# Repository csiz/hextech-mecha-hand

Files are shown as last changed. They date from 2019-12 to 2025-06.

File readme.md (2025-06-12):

Hextech Mechahand
=================

Full range of motion robotic hand with pressure, position and force sensors for $300 bill of materials.

Mechahand mk 14
---------------

Working on release candidate mk14. Using own motor drivers for fine force control, enhanced 
integrated sensor suite, completely refactored control code, easy USB connection, and 
improved manufacturing and repairability.

Mechahand mk 12
---------------

Patented design with integrated sensor suite! [GB2626014](https://worldwide.espacenet.com/publicationDetails/originalDocument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)

Mechahand mk 10
---------------

New design routes all cables and tendons through the center of the wrist, hiding them from
view and increasing the range of movement.

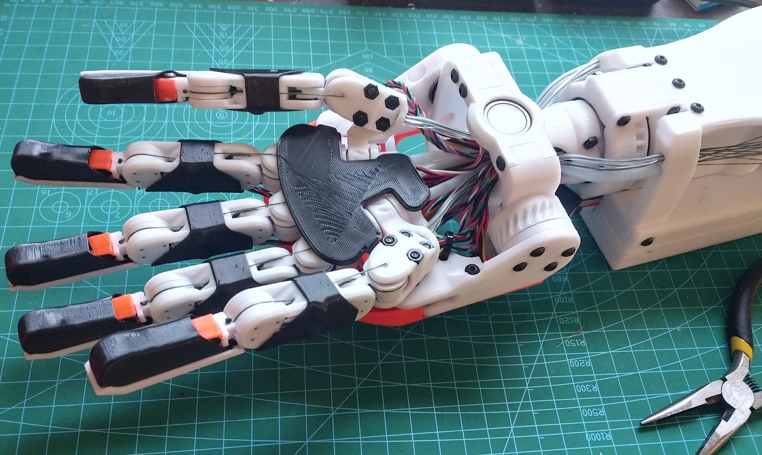
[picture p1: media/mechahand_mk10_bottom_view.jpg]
Mechahand mk 10.


Mechahand mk 9
--------------

Video of mk 9 picking up squish toy.

The Hextech mechahand is designed to be a low cost robot hand with a similar range
of motion as a human hand. It's targeted as an accessible standard for reinforcement
learning research. It has 20 degrees of freedom with position and force feedback on
each joint. The position encoders are placed in-situ allowing for accurate sensing
of the hand state regardless of the stretch on the tendons. Additionally there are
6 pressure sensors in the finger tips and palm for finer feedback. All electronics
plug into a compact PCB with current sensing for each actuated joint. The hand can
be controlled remotely by wifi using a force-limited PID loop. In the video, it's
mimicking my hand position in order to grasp an object. For autonomous control, a
custom force aware loop can be implemented.

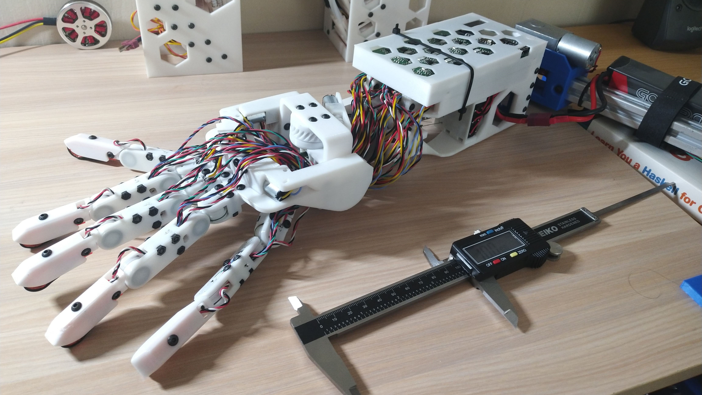
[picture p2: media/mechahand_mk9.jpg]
Mechahand mk 9.


The hand is built using off the shelf components and a 3D printed body at an amortized
cost of 300 USD per hand, requiring 30 hours of assembly time. Included in the cost
is the custom PCB designed for automated assembly. All design files for the mechanism,
the control circuit, and driver code is open source. Please open an issue wherever
[build instructions](build-instructions.md) need to be clarified.

Project layout
--------------

The project contains code for a 24 channel driver, the 3D printable model of the hand, and code to control the hand with a leap sensors. Details in the readme file of each folder.

* 24driver: Code and circuit design for a 24 channel PID controller with wireless interface and 12 pressure sensor inputs.
* hand_model: 3D model and instructions for the mecha-hand versions.
* leap_control: Code to control the hand via the leap motion sensor.

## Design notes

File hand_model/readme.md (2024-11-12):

Physical Mechahand Model
------------------------

1. No files for first iteration of mechahand, see [blog post](http://calin.mocanu.info/2019/06/11/mechahand-assemble.html) for pictures.
2. Mechahand II, the smallest hand version, failed due to pulley system cables passing through sharp corners. Can't have the cables passing through any corner as tensioning that wire causes large friction increase and a lot of plastic deformation of the nylon wire.
3. Mechahand III, the hand with the motors directly in the palm, failed because it's way too big and flimsy. Can't put motors on the fingers because they end up being too heavy and too big. Not way to cramp them tighter either. The 3rd version has a very modular design with each finger segment and wrist joint taken from 2 joint modules. Motorzied bigjoint is a sturdy and higher reduction joint for the wrist assembly. Motorized minijoint are perpendicularly geared joints as small as I can make with 1 motor and 1 potentiometer. Modularizing the hand was a good idea, and bigjoint is used in later versions.
4. Mechahand IV, first fully functional version, blog post pending. Uses the motorized bigjoint module for the wrist. There are direct drive joints with in-situ motors for the thumb and pinky opposable finger grasp. The rest of the fingers are controller by 1-sided pulley system; with the other side being a passive spring. With 2-sided pulleys on the old versions, there isn't enough tension on the string to gracefully unwind the side opposite the movement direction. We end up with loose wire coming out of the motor system and tangling up. There's no way to fix it without unreasonable tension on both sides. I therefore choose a single side pulley with a passive spring which keeps the system always in tension. We only need to be careful not to unwind when there's an external blocker.
5. Mechahand V, with neat finger shrouds! Fingers actuated again from 2 sides using the double pulley. Finger covers can hide the wiring to make it prettier. Using silicon wires leading to the motor system with a plastic soldering helper. Much neater to solder together, though putting the wires in place is difficult. Ok design on first sight, but multiple problems make it unusable. The little tubes are to stiff for the sideways finger wiggle. The printer springs are much too strong and have very little give. Difficult assembly requires a lot of force and moving about to get it to clamp down. When the clamp releases the spring fully extend and because the PTFE compression is too much. Overall too much friction to move the fingers when fully tensioned, and too little give in the tensioning system. Shrouds cover the wires though, will keep those. But thicker and mounted with screws so they can be used effectively.
6. Mechahand VI. First build and maybe usable hand! replaced the 6 to 1 buncher with 3 tube pairs that bunch into a single thick-ish tube leading to each joint. Also using much smaller springs for tension, this time acting directly on the tubes making a sort of piston. Neat, and mostly keeps the lines tensioned, but sometimes the spring goes in the tube, also small springs make for little give. Also have nicer tying mechanism on the nylon wire using a buckle of sorts. Pressure tip simplified for assembly by needing gauges on a single side that bends into an S shape. Sturdier finger covers too. Using the same soldering helper as V, but with thinner silicon wires. Unfortunately the wrist joint is propped stuck because of the large number of stiff PTFE tubes going to the fingers. The middle finger is also hard to bend because of the tube going to the tip joint. It's also hard to get consistent tension on the springs. If tensioned too hard it becomes stuck. Also because of the PTFE stiffness the 2 sides of a joint don't tension independently, which is the primary reason for the tensioning system, to prevent an unwind on the side that's relaxing.
7. Mechahand VII. Direct nylon pathing through center of joints. This design ditches the PTFE guides in favour of the direct pathing. Though still using the thick PTFE tube as a make shift piston for the new tensioning system. Instead of pushing 2 guide tubes apart, we now pull 2 end of the wire together. The wires slide past eachother to compress on a spring, guided by the thick PTFE tube and some plastic bits. Works with the long and easy to compress springs. When the plastic bits touch we also stop compressing the spring and can pass the full motor tension. Large springs means a large give, but hopefully not too much tension on the relaxing side. Can't test this hand until fully designed due to the tension being held by the hand structure. The hand structure is made much more rigid using proper bearings and thick plastic construction. Wrist pivots on bearings on both sides for structural integrity. Wrist roll now has the position potentiometer on a gear, and a large channel through the middle for the tendon wires. Removing battery from hand case, assuming external power source. Also to conserve space as new motor arrangement needs a lot of middle space for the tensioners. However no space on the side needed for the tensioning guides. Dropping the soldering helper in favour of dupont connectors for the fingers, and direct soldering for the motors. The extra connectors on the finger should help with assembly, as the finger cables can be separated from the motor.  Thicker plastic parts make for sturdier looking aesthetics, also the base cover. The middle covers, are also above some nuts and bolts and as packed as they can be, allowing for movement. Fingers crossed!
8. Mechahand VIII. Upgrade of mk 7 to fix weak wrist printing direction and thumb/pivot placement. Modified pivot worm joints to have a hole in the middle, like the wrist, to allow placing in line with the ring and index fingers. Much stronger placement, and keeps the distance between thumb/pinky and the wrist center constant; this is important to keep the tendons constant length. The ring finger is now fixed on the palm, as pivoting it together with pinky makes the leverage too large, and placement inconvenient. New placement also fixes the clearance issue with mk7. First hand version that really works!
9. Mechahand mk 9. Iterating on mk 8. Fingers now smaller and with integrated cover for the middle. The distance between the yaw and pitch joints halved to 15mm, making the joint closer to a ball joint. Unfortunately a true ball joint would require too much vertical thickness. Exploring design with magnetic sensors, but skipping for now. Thumb and pivot worm joints now smaller with lower gear ratio and bigger bearings. The 9mm bearings seemed like the weak points in previous design, hopefully now it's fixed. With smaller fingers, they are easier to place in the wrist and allows for nicer, smaller construction. Finger wires now go on the top, clearing the grasp of wiring. Wiring might look ugly as there's no hole to put them through, but placed mounting holes for an eventual cover. Finally tensioning using extension springs with a piece of nylon tied between the ends to cap the extended length. To pre-tension the tendons, we use the finger side loop of the spring as the hitch and the small buckle for simplified knotting; as an alternative to the hitch knot which doesn't hold on the thick nylon.
10. Mechahand mk 10. Pretty, buildable, and structurally sound mechahand! PTFE tubes brought back, but a short length passing through the wrist center needing minimal bending during wrist and thumb pivoting. Point of the tubes is to allow tendon tying from the outside, easing the build. Wrist hole substantially enlarged, allowing all electric cables and the tendon guides through. Designed ornate cover to hide wires. Designed tight-fitting skin out of TPU for the tip and mid finger, protects potentiometer cable connections, make hand grippier, neater! Bottom of fingers covered with a pressure sensor. Fingers shortened by 1cm, to near anatomical length. Moved case on top of wrist motor, compacting it by a bit. Should be a very presentable hand! (Spoilers... it was not presentable)
11. Mechand mk 11. New concept to integrate sensors in the palm and fingers. Designed a flexible circuit that folds into the hand shape and has integrated magnetic rotation potentiometers on the joints and pressure sensors on the fingertips. Now this is a presentable hand! The fingers are assembled from two parts that mesh with eachother and are held together by the flexible skin. The circuit is simply placed inside channels in the fingers and held in place by little clips. The wrist area now uses individual PTFE tubes for each actuated joint and there are indents designed into the palm and motor box to place the guide tubes. Still a lot of pain to assemble, the guide tubes rub on eachother as the wrist bends and might tangle the cable connection. The wrist stiffens up with the guide tubes in place and the tendons tensioned up... Unfortunate, but the flexible circuit with integrated sensors is a great idea!
12. Mechahand mk 12. Slight improvements to finger design to ease up assembly and strengthen weak points. Switching to coreless motors for quieter operation (true!). Now designing channels into the plastic of the motor box to guide the tendons directly but smoothly to each corresponding motor. Replaced the guide tube idea with directly connecting the tendons from motor box to the palm, however they pass through PTFE rings in the center of the wrist and at the beggining of the motor box to minimize friction and minimize the change in tendon length as the wrist bends. Unfortunately tensioning up the finger tendons now forcefully pulls the wrist to one side, and the motors are unable to overcome. The wrist was redesigned with bevel gears (partially filled with gear teeth) for easier assembly than the purely wire driven differential. Also using bevel gears for the finger pivot action, again for ease of assembly. Electric wire now shielded by a flexible plastic channel when passing through the wrist channel.
13. Mechahand mk 13. Changing from double sided tendons for the finger joints to single side tendon for flexion and spring for finger extension. Switching the knuckle actuation from actuating the pitch and yaw separately to actuating both diagonally (similar to the differential). Big improvement in precision after this change, although more complex driving mechanism to avoid unspooling! More improvement to finger design, thickenned up fingers for strength and created stubbier finger models for the thumb and pinkie. Changed palm design to also use springs for the pivot actions and enlarged the top cover to cover everything nicely. Solved the wrist guide problem by designing a guide channel made of stiff segments with channel holes held together by a flexible snake connecting the motor box and palm. The flexible core forces the guide plates into bending smoothly with the movement of the wrist. This wrist design finally has the full range of movement that it was designed for and is able to move when the fingers move (not locked in place by the tendon tension). Also, since the fingers are driven from a single side, the bias on the wrist from the finger actuation is more predictable. This robot hand works!

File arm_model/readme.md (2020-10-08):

Hextech Mecharm
===============

4 DOF robotic arm to drive the upper arm half of the robot hand. Ball like joint using
a differential gear on the shoulder, separate motor for arm twist motion, and another
motor for the elbow. Using 3D printed cycloidal drives and a 5010 brushless motor used
in large drones, but low 360KV.

TODO:
-----
[ ] Fix elbow motor, I think star connection not properly soldered.
[ ] Place and wire potentiometers too.
[ ] Drive motors using the RTM library of the ESP32.

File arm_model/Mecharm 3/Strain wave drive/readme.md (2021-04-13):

Strain wave drive
-----------------

Backdriveable strain wave drive with 30x and 42x reduction ratios.

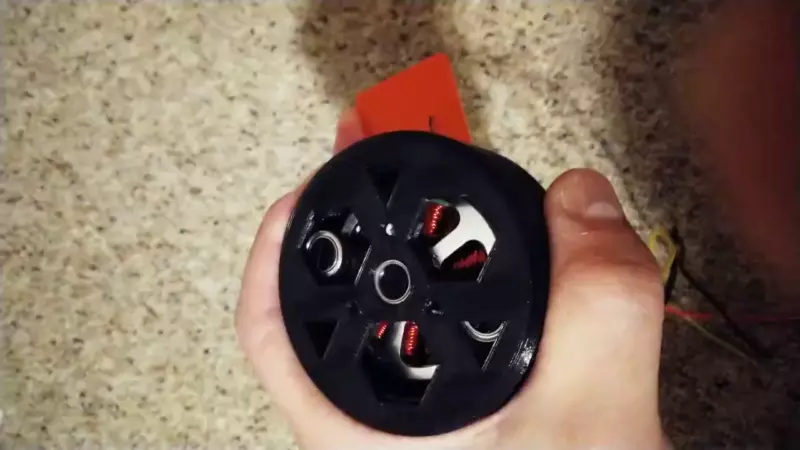
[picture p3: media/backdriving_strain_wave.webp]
Video of strain wave being rotated manually.


Compact construction with flex spline cup surrounding the motor. Drive size is 70mm diameter and 32mm height. Printed in PETG, including the flex spline.

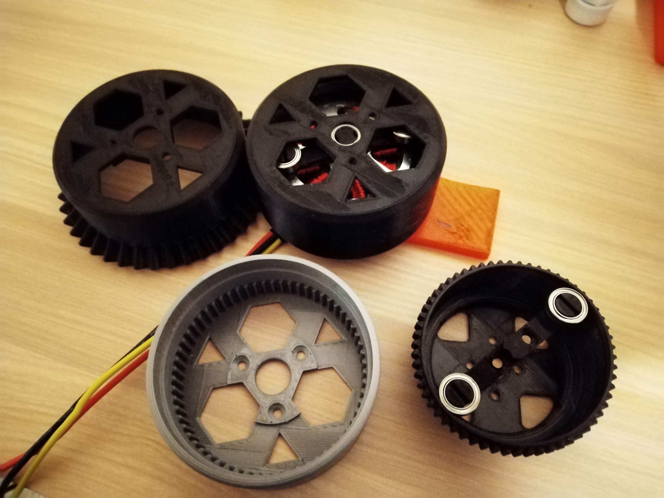
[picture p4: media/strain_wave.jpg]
Strain wave drive.


Components:
  * 1 - 5010 brushless motor
  * 1 - 6810 ball bearing
  * 3 - MR128 ball bearings

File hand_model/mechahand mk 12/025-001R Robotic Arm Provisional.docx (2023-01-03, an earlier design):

UNITED STATES PROVISIONAL PATENT APPLICATION

of

Calin Mocanu

for

A SYSTEM OF ROBOTS AND ROBOTIC PARTS INCLUDING METHOD OF CONSTRUCTION AND METHOD OF USE

A SYSTEM OF ROBOTS AND ROBOTIC PARTS INCLUDING METHOD OF CONSTRUCTION AND METHOD OF USE

FIELD OF THE INVENTION

[001] This application relates to the design and construction of robotic parts, and more particularly, improvements in functionality and improvements in compact designs for robotic parts.

# BACKGROUND OF THE INVENTION

[002] Humans have been trying to create robots for decades, but with only limited success. Robotic parts such as arms, wrists, and hands suffer from a number of drawbacks and limitations. One of the drawbacks in the field of robotics currently is a limitation on the ability to reduce the size of various features.
[003] As an example, small jointed parts like fingers need to carry numerous sensors, such as pressure sensors joint position sensors, etc. And, in addition to the sensor itself, each sensor has various wires, wiring harnesses, connectors, etc. that must be carried through the fingers, including tight places like knuckle joints. As used herein, the term “wire” can refer to single strands or multiple-strand wires that are insulated with insulating material surrounding the conductive strand(s). The insulating material around the strand is flexible, and the strand with the insulation around it can be bent into various paths throughout an electronic device. However, the strand plus the insulating material around it that form a wire can become bulky when multiple wires are used in the same device or routed along the same path. The terms “wiring harness” can refer to physical connectors that allows two insulated wires to be connectively joined to form a single electric conductor through the use of Newtonian force, including connectors that can connect multiple sets of insulated wires at the same time. Wire harnesses are typically made of insulated metal wires that must be attached to connectors on both sides. The wire harness can then be plugged into corresponding connectors on two circuits, connecting them electrically. This requires that both wires have a connector or harness. These harnesses or connectors can be clips mounted at the end of the conductive strands so that a user can forcefully engage two clips or other connectors together to form a conductive strand that conducts electricity and electric signals through the clip from one strand to the other, thereby forming a single conductive path. To join two wires into a single conductive path, a wiring harness must be applied to both wires, which can be a costly and difficult step in manufacturing as the insulation must be stripped from the end of the wire, the wire must be connected to the harness, etc. For each connection end the electrical insulation must be stripped, then the wire is crimped into pins, then the pins must be inserted into the plastic male connector. This must be done for every end of every wire.
[004] These connections where the end of the wire is connected to a wiring harness create a weak point along the electrical path, and as the wire is flexed back and forth repeatedly in normal usage, the wire is most likely to break at the connection with the wiring harness that allows the two wires to be joined. The places where the wires connect to the harnesses tend to see the most stress, and the wires tend to fail at the places where they are connected to the harnesses. Furthermore, after the two harnesses are linked together, they take up a large amount of space inside the device. When this is multiplied by a large number of wires, the result is either a large number of bulky wires and wiring harnesses that must take up space, or a smaller number of larger multi-wire harnesses that take up more space.
[005] A highly functional robot finger would ideally be able to sense pressure at the tip of the finger, the back of the finger, both sides of the finger, and of course, the inner finger pad where the finger makes contact with an object being gripped by the robot’s hand. However, this requires a multitude of bulky sensors, wires, wiring harnesses, and circuit connectors, that must all be packed into a small finger, while also allowing the finger to bend and move. This means that parts such as fingers must be at least a minimum size that is often larger that desired for various applications. Furthermore, as the manufacturer attempts to reduce the overall size of the finger to the minimum size capable of carrying all of the necessary components, the space inside the finger gets more and more crowded, and therefore more and more difficult for the manufacturer to assemble all of the components inside of the tight space. All of this contributes to ever increasing costs as manufacturers attempts to reduce the size of various parts given the constraints of current technology.
[006] In some cases, in order to reduce the size of the fingers, it has been necessary to reduce the number of sensors, the quality of sensors, and/or the types of sensors. This means that there is often a direct correlation between decreasing size of parts such as fingers and decreasing functionality. Manufacturers may also reduce the quality or strength of other parts such as fingers and wrists in order to allow for decreased size, but this decreases in quality, such as decreasing the robustness of hinges and hinged parts, results in inferior products that break easily.
[007] In some cases, the size has been reduced by attempting to remove some components such as sensors from tight parts such as fingers. This can be reducing the number of pressure sensors, but can also mean attempting to measure certain variables such as fingertip position from alternate locations outside of the fingertip. For example, some manufacturers have attempted to measure finger position by placing magnets in the finger tips, and then sensing the proximity of the magnet to other parts such as a palm of a robotic hand. Moving the sensing activity to the palm means there is more space for these sensors. However, this also results in a significant reduction in quality. Placing magnets in the fingertips can have an effect on the robot’s ability to grasp and release magnetic objects, but even worse, grasping and releasing magnetic objects will interfere with the sensor’s ability to accurately know where the fingertips are positioned. Furthermore, although ample space may exist in a palm area, magnets in the fingertips take up valuable space used for pressure sensors and may interfere with the remaining pressure sensors.
[008] Other manufacturers have attempted to measure position by monitoring the positions of servos in the arm that control the fingers through tendons. However, this can be extremely unreliable. The tendons that connect to the finger tips can stretch over time, resulting in inaccurate readings, and as the tendons pass through the narrow and crowded finger knuckles, even slight interactions with other components such as wires and wire harnesses can lead to inaccurate results. As wires and wiring harnesses interfere with the path of the tendons, the length of tendon does not exactly correlate to finger position. In the state of the current technology, measuring the position of the fingers by monitoring the rotational position of the servos in the arm that drive the fingers is the best option, given that the measuring can occur outside of the finger and reduce the size constraints of a finger, but this method of measuring finger position is prone to inaccuracy.
[009] Various other means also exist for more accurately measuring the rotational position of the joints, and therefore the position of the fingertip, or wrist, or arm, etc. However, to date, either these means produce inaccurate results or have not been reduced in size sufficiently to allow their use in a robotic finger knuckle that can be the size of a human finger while also allowing for tendons wires, and wiring harnesses to exist in the same space.
[0010] Up to now, there has been a trade off between various aspects, including the quality of sensing, the number of sensors and the amount of sensed data, the size of the finished parts, and the cost to assemble. For example, as size decreases, the quality of components such as sensors and/or the number of sensors decreases and/or the cost of assembly increases. Furthermore, there are hard limits on the ability to reduce size while still maintaining even a minimum level of sensing at any cost. The same can be said about improving the quality and/or number of sensors, which then increases size and cost, and the same can be said about reducing cost which then results in reduced sensing and increased size. Similarly, the quality of parts such as fingers and wrists can be part of the trade-off, and reducing the robustness of components such as hinges and knuckles can allow for reduced size, but with a corresponding reduction in quality. Improving one of these aspects seems to come at the cost of the others.
[0011] It would be desirable to have new robotic technology and new components that allow robotic parts such as fingers, wrists, arms, etc. to be reduced in size to the size of human fingers, wrists, arms, etc, or smaller, while also maintaining robust pressure sensing and position sensing, reducing costs, and maintaining strong parts and components. It would be further desirable if the new robotic technology and new parts result in reduced cost of components and reduced cost of assembly while also allowing for reduced size at the same time.

# SUMMARY OF THE INVENTION

[0012] This invention overcomes disadvantages of the prior art by providing a system and method for manufacturing robotic parts, including parts that can be analogous to fingers, hands and arms. The system and methods described herein include various ways to reduce the cost of manufacturing, reduce the size of manufactured parts, and increase the reliability and quality of sensed data. These improvements include producing capacitive pressure sensors that are simple in construction and can be manufactured by folding a sheet of material over itself to form a sandwich around a double-sided adhesive. These force sensors are simple and cheap to manufacture, and can be connected to cheap touch sensor chips. The sheet of material can also be a Flexible Circuit Board (FCB) that can connect the sensor to other electronic components, including touch sensor chips and processors. The touch sensor chips can be Integrated Chips (IC) that can be integrated on the FCB, and the IC(s) can be located near the force sensors on the FCB. The FCB can also include multiple sensors on the same FCB, so that, for example, multiple sensors in a finger such as finger tip, sides of the finger, back of the finger, etc, can all be manufactured as part of the same FCB, and can all be connected to the touch sensor chip(s) integrated on the FCB. With all of the sensors and circuits manufactured as a single FCB, the finger can be constructed with no wiring harnesses or other bulky connectors to be connected during manufacturing or taking up space inside narrow parts like a finger. The single FCB can then be arranged through a finger, including through narrow joints such as knuckles, and can be tied into place within a finger, held in place with clips, etc, and can connect sensors to a processor with very little space requirements, leaving space within a small finger for further components. Because the FCB is free from insulation, there is no rubber or other insulation within the fingers to get caught up on moving parts or prevent tendons from sliding freely. The flex circuit connectors can be printed in the same process required to make the circuit board. The connectors can be electrical traces as any other on the FCB, with exposed and plated pads on the end, using the same process used to make the pads of most components on the circuit board. The flex circuit can then be directly inserted into the female connector on the palm. The connector can also be thinner because the flex circuit is thinner than wire connectors.
[0013] Additionally, sensors such as rotational position sensors, also referred to as rotational encoders, can be configured to be integrated with the FCB, thereby eliminating the need for additional wires, wire harnesses, and other connectors. These rotational position sensors can be used to measure the rotational position of hinged joints such as finger knuckles. These sensors can utilize the Hall effect to measure the orientation of a diametrically magnetized magnet that can be assembled in a stack with the axis of the magnet on the same axis as the knuckles or other hinges. This approach with stacking a disc shaped magnet and rotational position encoder on axis with the knuckle hinge allows for a small and flat rotational sensor that takes up little space while still reporting rotational position with accuracy. The rotational sensor can also be configured to integrate with the FCB to provide measured data to the processor without the need for additional wiring. The space savings that result from the innovative design of this sensor combined with the space savings that result from the FCB replacing traditional connection types allows for the use of on-axis hall sensors which are significantly more accurate than prior art position sensors for robotic parts.
[0014] The use of this precise on-axis rotational position sensor also allows for the use of a 4-bar linkage system for torque sensing. The 4-bar linkage torque sensing system can allow a processor to calculate the pressure being applied to a held object by a finger. A processor can measure minute divergence, or flexing, of finger components by measuring and comparing the rotational position at multiple joints at the same time. As applied pressure increases, so too does the flex in certain components, which can be determined by measuring the rotational positions of multiple joints at the same time. The applied pressure can be determined from the amount of flex. Calculating the applied pressure when a fingertip is in contact with an object means that a pressure sensor such as a capacitive pressure sensor does not need to be used at the fingertip, thereby further reducing the space requirements in the finger while also decreasing production cost.
[0015] In an embodiment, a robotic component can include a FCB that can include at least one capacitive force sensor, the capacitive force sensor being unitary with the FCB, and the capacitive force sensor having two electrodes folded around a compressible dielectric pad, and at least one rotational position encoder, the rotational position encoder being on the FCB as an Integrated Chip (IC), and at least one magnet, the at least one magnet being embedded in a joint of the robotic component so that the at least one magnet and the at least one rotational position encoder are on-axis with the joint, so that the rotational position encoder can determine the rotational position of the magnet within the joint.
[0016] The FCB can include at least one strain relief loop that passes around a loop holder within the robotic component. The FCB can include at least one bending segment, the bending segment allowing the FCB to be folded into multiple planes. The at least one rotational position encoder can include at least two rotational position encoders, and wherein the FCB can be bent so that a first rotational position encoder is in a first plane and measures a rotational position around a first axis, and a second rotational position encoder is in a second plane and measures a rotational position around a second axis, wherein the first axis and the second axis are in different planes. The FCB can include at least one knot segment, wherein the knot segment is tied in a knot around a support within the robotic component. The joint of the robotic component can have a hollow central canal that passes through the center of the joint, including passing through the rotational axis of the joint, and wherein the FCB passes through the hollow central canal and the rotational axis of the joint. The robotic component can also include a layer of foil between the at least one capacitive sensor and the outside of the robotic component, the layer of foil shielding the capacitive sensors from external capacitance. The robotic component can include a 4-bar linkage system, wherein a motor that powers the movement of one joint will also power the movement of a second joint through the 4-bar linkage, and wherein a linkage bar can be semi-rigid, so that a quantity of force applied to a finger tip can be calculated from the rotational position of the two joints when the linkage bar is flexed under force. The FCB can be tied in a knot around the linkage bar. The joint of the robotic component can have a hollow central canal that passes through the center of the joint, including passing through the rotational axis of the joint, and wherein tendons that control the movement of the robotic component are routed through the hollow central canal and the rotational axis of the joint. The robotic component can have multiple FCBs in different portions of the robotic component, and the multiple FCBs can be connected together by FPC connectors and can be connected free of soldering or wiring harnesses. The FCB can include holes through the FCB and wherein tendons that control the movement of the robotic component can be routed through the holes through the FCB.

BRIEF DESCRIPTION OF THE DRAWINGS

[0017] The invention description below refers to the accompanying drawings, of which:
[0018] Fig. 1 is a perspective view of a robotic finger, according to an illustrative embodiment,
[0019] Fig. 2A is an upper perspective view of circuitry, including sensors, from inside the robotic finger of Fig. 1, according to an illustrative embodiment;
[0020] Fig. 2B is a lower perspective view of the circuitry of Fig. 2A also showing the position of knuckle magnets, according to an illustrative embodiment;
[0021] Fig. 3 is a top view of the circuitry of Fig. 2A, shown in a flat conformation before the sensors are folded and before the FCB is arranged into the shape used inside the finger of Fig. 1, according to an illustrative embodiment;
[0022] Fig. 4A is a side view of the circuitry of Fig. 2, showing pressure sensors folded into the sensing conformation, according to an illustrative embodiment;
[0023] Fig. 4B is a detailed view of the pressure sensors shown in Fig. 4A, according to an illustrative embodiment;
[0024] Fig. 4C is a cross sectional view of the sensors shown in Fig. 4A, taken along cross section line 4C-4C of Fig. 4A, according to an illustrative embodiment;
[0025] Fig. 5A is a bottom perspective view of a finger, according to an illustrative embodiment;
[0026] Fig. 5B is a side view of the finger of Fig. 5A, shown without the outer shell, according to an illustrative embodiment;
[0027] Fig. 5C is a cross section of the finger of Fig. 5B, taken along cross section line 5C-5C, and viewed from below, according to an illustrative embodiment;
[0028] Fig. 5D is a bottom perspective view of various components inside of the finger of Fig. 5A, including structural components, and showing the placements of magnets for rotational sensors, according to an illustrative embodiment;
[0029] Fig. 5E is a detailed view of the area of detail 5E in Fig. 5C, showing an arrangement of joint components within the bone, according to an illustrative embodiment;
[0030] Fig. 6A is an exploded bottom perspective view of various components inside the finger of Fig. 5A, including multipurpose clips that can maintain the positions of rotational sensors and the FCB; according to an illustrative embodiment;
[0031] Fig. 6B is a side view of various components inside the finger of Fig. 5A, showing rotational sensors held in place by the clips and showing the arrangement of the FCB and magnets; according to an illustrative embodiment;
[0032] Fig. 7A is a schematic diagram of a 4-bar linkage system that can use magnetic rotational sensors to determine torque and pressure, shown with the finger in a straight conformation, according to an illustrative embodiment;
[0033] Fig. 7B is a schematic diagram of the 4-bar linkage system of Fig. 7A, shown with the finger in a bent conformation and without applied pressure, according to an illustrative embodiment;
[0034] Fig. 7C is a schematic diagram of the 4-bar linkage system of Fig. 7B, shown with pressure applied to an outer, fingernail side of a finger, thereby flexing the linkage bar in a shortened conformation; according to an illustrative embodiment;
[0035] Fig. 7D is a schematic diagram of the 4-bar linkage system of Fig. 7B, shown with pressure applied to an inner side of a finger, thereby flexing the linkage bar in an elongated conformation; according to an illustrative embodiment;
[0036] Fig. 8A is a perspective view of the interior of the robotic finger of Fig. 8A showing the components of the 4-bar linkage system, according to an illustrative embodiment;
[0037] Fig. 8B is a top view of the partial robotic finger shown in Fig. 8A, according to an illustrative embodiment;
[0038] Fig. 8C is a cross section view of the partial robotic finger of Fig. 8B, taken along cross section line 8C-8C, showing the finger in a straight conformation, according to an illustrative embodiment;
[0039] Fig. 8D is a cross section view of the partial robotic finger of Fig. 8B, taken along cross section line 8C-8C showing the finger in a bent conformation, according to an illustrative embodiment;
[0040] Fig. 9 is a perspective view of an assembled robotic hand, including a wrist, palm, and fingers, according to an illustrative embodiment;
[0041] Fig. 10 is a perspective view of the circuitry, including sensors, from inside the robotic hand with fingers, according to an illustrative embodiment;
[0042] Fig. 11A is a perspective view of the circuitry, including sensors, from inside of a robotic palm shown without fingers, according to an illustrative embodiment;
[0043] Fig 11B is a top view of the circuitry of Fig. 11B, shown in a flat conformation before the sensors are folded and before the FCB is arranged into the shaped used inside the palm of Fig. 9, according to an illustrative embodiment;
[0044] Fig. 12A is an exploded perspective view of the top of a partially assembled palm, showing circuits, sensors, and removed back cover, according to an illustrative embodiment;
[0045] Fig. 12B is an exploded perspective view of a partially assembled palm, showing circuits, sensors, and removed hand bottom cover, according to an illustrative embodiment;
[0046] Fig. 13A is a partially assembled view of a hand, showing thumb and pinkie joints and thumb and pinkie joint rotational position sensors, according to an illustrative embodiment;
[0047] Fig. 13B is a detailed view of a pinkie joint of Fig. 13A, showing an arrangement of bevel gears, according to an illustrative embodiment;
[0048] Fig. 13C is a detailed view of the pinkie joint of Fig. 13B, showing a rotational position sensor within the joint, according to an illustrative embodiment;
[0049] 14A is a perspective view of the wrist of Fig. 9, showing the hollow central channel that can accommodate tendons and FCBs, according to an illustrative embodiment;
[0050] Fig. 14B is a perspective view of selected components within the palm of Fig. 12B and the wrist of Fig. 14A, showing bevel gear components, according to an illustrative embodiment;
[0051] Fig. 14C is an exploded view of the left bevel gear and outer structure of the wrist of Fig. 14B, showing a rotational position sensor; according to an illustrative embodiment;
[0052] Fig. 15 is a method of manufacturing a robotic finger, according to an illustrative embodiment;
[0053] Fig. 15B is a method of manufacturing a robotic hand, according to an illustrative embodiment;
[0054] Fig. 16 is a method of sensing force using a capacitive sensor, according to an illustrative embodiment;
[0055] Fig. 17 is a method of sensing force using rotational position sensors, according to an illustrative embodiment; and
[0056] Fig 18 is a schematic view of a robot control processor, according to an illustrative embodiment.

DETAILED DESCRIPTION

[0057] There are a great many possible implementations of the invention, too many to describe herein. Some possible implementations that are presently preferred are described below. It cannot be emphasized too strongly, however, that these are descriptions of implementations of the invention, and not descriptions of the invention, which is not limited to the detailed implementations described in this section but is described in broader terms in the claims.
[0058] As used herein, the term robotic finger refers to a robotic part that can include force sensors, joints, joint position sensors, and flexible circuit boards (FCBs). Although the robotic finger described herein is similar in appearance and function to a human finger, the technology described herein is not intended to be limited to human forms. Similarly, as used herein, the terms robotic hand, palm, and wrist refer to robotic parts that include force sensors, joints, position sensors, and FCBs, and although the robotic parts described herein are similar in appearance and function to the human body, the technology described herein is not intended to be limited to human forms.
[0059] Fig. 1 is a perspective view of a robotic finger, according to an illustrative embodiment. A robotic finger 100 can have a base 108, and multiple phalange segments including distal phalange 102, middle phalange 104, and proximal phalange 106. Phalanges 102 and 104 can be separated by joint or knuckle 112, and phalanges 104 and 106 can be separated by joint or knuckle 114. Knuckles 112 and 114 can bend or curl inward along arrow A and arrow B, respectively. Phalange 106 and base 108 can be separated by joint 116 that can bend or curl along arrow C, and phalange 106 and base 108 can also be separated by joint 118 that can bend or yaw along arrow D. Joints 116 and 118 allow phalange 106 to move relative to base 108 along two different axis. It should be clear that in various embodiments, larger or smaller numbers of phalanges are possible, with joints between each phalange, and it should be clear that any two phalanges can have one or more than one joint between them thereby allowing for one or more than one axis of movement between any two phalanges.
[0060] The design described herein allows for the finger, including joints, to have a very small form factor. In various embodiments, the finger, including joints, can have a maximum width FW of 16 mm or less. In various embodiments, the finger can have a maximum height FH of 18 mm or less. In various embodiments, a finger knuckle can have a maximum knuckle height KH of 20 mm. The reduced size is possible in part due to the absence of wiring and wiring harnesses throughout the finger, along with the compact design for the knuckle rotational position sensors. The finger can be fully functional with capacitive force sensors in four directions, knuckle rotational position sensors, and a torque force sensor, all within the compact design having a maximum finger width of 16 mm, a maximum finger height of 18 mm, and a maximum knuckle height of 20 mm.
[0061] In traditional designs, pressure sensors in a finger would require a separate sensor unit for each touch sensitive area, and each pressure sensor unit would have wires extending from the sensor so that each of the sensors can be connected to a controller. In some cases this could include bulky wiring harnesses or connectors. The design described herein has a number of pressure sensitive areas without the need for wires or wiring connectors. The finger 100 shown in Fig. 1 can have four pressure sensors that can sense pressure at pressure sensitive areas 122, 124, 126, and 128, however, different numbers and configurations of pressure sensors are possible.
[0062] Fig. 2A is an upper perspective view of circuitry, including sensors, from inside the robotic finger of Fig. 1, according to an illustrative embodiment, and Fig. 2B is a lower perspective view of the circuitry of Fig. 2A also showing the position of knuckle magnets, according to an illustrative embodiment. Finger circuitry 200 can include a finger FCB 202, finger tip force sensors 222, 224, 226, and 228, and rotational position encoders 212, 214, 216, and 218. As used herein, the terms “rotational position encoder,” “rotational encoder,” and “contactless potentiometer” can be used interchangeably. Finger tip sensor 226 can sense force on the back of the finger, in a location associated with a fingernail in a corresponding human finger, and finger tip sensor 224 can sense pressure on the distal tip of a finger tip. Finger tip sensor 222 can sense pressure on a first side of the finger, and finger tip sensor 228 can sense pressure on a second side of the finger, opposite from the first side. Although this description describes specific sensors in specific locations, and describes them in the context of similarity to human fingers and human sensing locations, it should be clear that this is merely illustrative, and various numbers and arrangements of sensors are possible.
[0063] Rotational position encoder 212 can sense the rotational position of the diametrically magnetized magnet embedded in the knuckle 112, and can therefore detect the rotational position of the knuckle 112. or put another way, can detect the angle of the joint between distal phalange 102 and middle phalange 104. Rotational position encoder 214 can sense the rotational position of knuckle 114 between phalanges 104 and 106. Rotational position encoder 216 can sense the rotational position of knuckle 116 between phalange 106 and base 108 as phalange 106 curls inward toward the palm, and rotational position encoder 218 can sense the rotational position of joint 118 as phalange 106 moves in a yaw direction relative to base 108. A diametrically magnetized magnet, such as diametrically magnetized disc magnet 232, 234, 236, and 238 can be positioned in each joint, and the encoder can detect the rotational position of the magnet. As used herein, the term “diametrically magnetized magnet” refers to a magnet that is magnetized across the diameter, with the poles located on the curved surfaces along the outer circumference of the magnet. The magnets shown in Fig. 2B are shown in proximity to the corresponding rotational encoders, however, it should be clear that the magnets are fixed within the joints and move with the joints relative to the encoders, so that the encoders can detect the rotational position of the magnets, and thereby detect the rotational position of the joints.
[0064] Taken together, the rotational position encoder and diametrically magnetized magnet form a rotational position sensor. The rotational position encoder can be an integrated chip (IC) on the FCB that can calculate and digitize the angle. The rotational position encoder can include 4 analog hall effect sensors arranged on the IC of the FCB in a circle around the axis center. The chip can interpolate the analog signals and perform basic trigonometric math right there on the IC. The output of the IC that is the rotational position encoder can be a digital angle, and that digital angle data can be transmitted through traces on the FCB.
[0065] The rotational position encoders and the force sensors can be integrated as part of the FCB. Integrating sensors such as sensors 222, 224, 226, and 228, rotational encoders 212, 214, 216, and 218 as part of the FCB allows for a design that is free from insulated wires and wiring harnesses. The FCB can include separate conductive traces for each sensor, including force sensors and rotational position sensors, and can connect each sensor to circuits and processors located outside of the finger without the need for additional connectors or wires within the finger. By having all of the sensors connected to circuits and processors outside of the finger through fine traces on a single FCB, the physical volume of all connections from sensors in the finger to connections outside of the finger is substantially reduced, allowing for much smaller form factor fingers, while also allowing for reduced assembly cost because all rotational encoders and force sensors in a finger can be already pre-manufactured together in a single finger circuit unit 200.
[0066] The FCB 202 can be routed through narrow spaces in an articulated finger, including though the narrow spaces inside a joint or knuckle. However, as different joints move and move in different directions, different forces can be exerted on the FCB in different directions. To overcome this problem, a series of strain relief loops can be folded into the FCB, such as strain relief loops 244, 246, and 248. These strain relief loops provide extra slack in the FCB, so that the overall length can lengthen and shorten as necessary, without the FCB getting tangled or getting in the way of other components. The loops can be wrapped around loop-holders (not shown) throughout the path of the FCB, including within the finger or other components, explained more fully below.
[0067] Additionally, the FCB can be tied in place, such as FCB knot 242. FCB knot 242 can be tied around a structural component (not shown) within the finger or other component, and can secure the FCB in place within the finger while the various finger components move in different directions and exert various forces on the FCB. In various embodiments, the knot 242 can be tied around a linkage bar within the finger, explained more fully below. Because the FCB itself is flexible and can be physically tied into a knot, it can be secured in place in a way that allows flexible motion of the finger and the FCB without the need for bulky attachment devices or circuit routing components.
[0068] Fig. 3 is a top view of the circuitry of Fig. 2A, shown in a flat conformation before the force sensors are folded and before the FCB is arranged into the shape used inside the finger of Fig. 1, according to an illustrative embodiment. Turning now to Figs. 1, 2A, 2B, and 3, strain on the FCB can further be reduced by having at least a portion of the FCB be split along the length, so that the FCB can more easily be flexed in different directions without bowing, binding, or kinking. Having a split 252 in an FCB 202 can be particularly valuable in places where multiple joints between the same segments allow for bending along different directions, or through three dimensions. By way of non-limiting example, the split 252 can allow a first side 254 to move and flex independent of second side 256. When proximal segment 106 moves along arrow C and along arrow D relative to base 108, the two narrower sides can move independently more freely and more flexibly compared to a single FCB having the combined width of 254 plus 256.
[0069] The FCB can be designed to fold into nearly any shape. As shown in Fig. 3, there can be one or more 90-degree turns such as 90 degree turn 282 before the FCB turns into two strands 254 and 256 that pass through the knuckles 116 and 118. Combined with a 90-degree bend at bending zone 284, the FCB path can route along the sidewall of the middle segment, then turn and route along a different direction through the knuckles 116 and 118. Similarly, 90 degree turn 286 and a 90 degree bend at bending zone 288 allow the FCB to exist in one plane in one place in the finger, and turn to route along another plane 90 degrees away. When the FCB is bending at a bending zone or flexing through a knuckle, it is flexing along a direction in and out of the page as shown in Fig. 3, or put another way, the very thin dimension is bending around a curve, while the wider dimension does not need to bend. The 90 degree turns help to allow the FCB to be folded in such away that the flat dimension bends through knuckles 112 and 114, while segment 276 the FCB can be offset 90 degrees and routed vertically though the side of the middle segment. Similarly, knot section 350 can have angles 352 and 354 that allow the FCB to be bent and tied, and then continue to route through the next knuckle with the flat dimension oriented to bend around the axis of rotation of the knuckle. Tabs 362 and 364 can help to secure the knot together when it is tied around the flex rod.
[0070] The same FCB is shown in Fig. 3 in a flat conformation after manufacturing of the FCB, and shown in Figs. 2A and 2B in the folded conformation as it is found inside the finger of Fig. 1. Each pressure sensor, such as pressure sensor 222, is a capacitive force sensor that includes two electrodes: 312 and 322. Electrodes 312 and 322 are unitary parts of the single circuit unit 200. Distal electrode 322 can be folded over at hinge 332 so that distal electrode 322 can be nearly in contact with proximal electrode 312. Electrodes 312 and 322 can be held nearly together, while also being held just slightly apart, in the folded conformation with a compressible dielectric pad 262, such as double sided adhesive or double sided tape, to form an adjustable capacitor. The compressible dielectric pad 262 should be elastically compressible, should be an insulating dielectric material, and can have a thickness that can be between 0.2 mm and 2 mm. The compressible dielectric pad 262 can have adhesive on both sides, such as a double sided tape, and as used herein, the dielectric pad can be referred to as a compressible dielectric double sided tape, or double sided adhesive. However, although having adhesive on both sides increases the convenience of manufacturing, it should be clear that adhesive can be applied separately, and the pad does not need to be a double-sided tape. However, as used herein, in the interest of a clear description, the compressible dielectric pad may also be referred to as a dielectric double-sided tape, or compressible dielectric double-sided adhesive.
[0071] Traces in the FCB can connect the sensor to a capacitance-to-digital converter chip, also referred to herein as a touch sensor chip, such as Integrated Chip (IC) 270 so that changes in capacitance can be measured as the tape gets squished and the two electrodes on each side 312, 322 come closer together. When a compressive force is applied to the capacitive force sensor 212, the distance between electrodes 312 and 322 decreases, which changes the capacitance. By measuring the capacitance, we can measure the pressing force using an IC 270 that can be on the same circuit board connected to the electrodes. In various embodiments, the touch sensor IC 270 can be centrally located at a hub between pressure sensors. In various embodiments, the touch sensor IC can be positioned within a central cavity of a finger tip, as shown in Fig. 2B, so that it is close to the force sensors and in a location where space is at less of a premium.
[0072] Similarly, sensor 224 can be made by folding electrode 324 over electrode 314 at hinge 334 and using compressible dielectric adhesive 264. Sensors 226 and 228 can also be made by folding the electrodes around a compressible dielectric adhesive such as a double sided tape. In various embodiments, multiple capacitive force sensors, such as sensors 222, 224, 226, and 228 can be connected to the same IC 270, and the sensors can be arranged around the fingertip to measure forces from multiple sides.
[0073] This arrangement creates a compact design that can measure a quantity of force being applied from multiple different directions. It can also be assembled quickly and at little cost by folding the electrodes over the double sided tape to form sensors that are part of the unitary circuit unit 200. This requires nothing more than a piece of sticky tape and folding the circuit. The sensor can be created by folding a single flexible circuit board, which eliminates the need for multiple circuit boards sandwiched together and connected by wires. Furthermore, there is no need to create one of the electrodes by other means such as coating a surface with an electrically conductive layer that can be difficult to manufacture. Multiple sensors can be folded from the same flexible circuit board, thereby creating a 3D sensing array. The sensors are also integrated with the rest of the circuit. Because the electrodes are folded from the same flexible circuit board that contains the integrated chips, the electrical connections can be printed directly onto the circuit. This further reduces the cost of the materials, the cost of manufacturing, and the size of the unitary circuit unit 200. The unitary circuit unit can be a component within a finger while taking up very little space within the finger and thereby allowing for additional functional components within the finger, such as rotational position sensors within the joints. The folded sensor can be an elegant and compact design that is free of unnecessary parts that take up space or unnecessary assembly steps. A sensor can be made of two electrodes that are unitary with the FCB and folded over a compressible dielectric pad, free from additional components or connections.
[0074] Fig. 4A is a side view of the circuitry of Fig. 2, showing pressure sensors folded into the sensing conformation and showing area of detail 4B and cross section line 4C-4C, according to an illustrative embodiment. Fig. 4A shows fingernail force sensor 226, fingertip force sensor 224, and first side force sensor 222. Rotational position encoders 212, 214, 216, and 218 are also shown. The circuit unit 200 is shown in Fig. 4A as it is found in a finger when it is fully installed within the finger. A Flexible Printed Circuit Board connector (FPC connector) 204 is used to connect the FCB 202 of the finger to the circuits of the palm, explained more fully below. The FPC connector 204 can be printed in the same process required to make the circuit board. The connectors 204 can be electrical traces as any other on the FCB, with exposed and plated pads on the end, using the same process used to make the pads of most components on the circuit board. The flex circuit can then be directly inserted into the female connector on the palm. The FCB of a finger can be connected to the FCB of the palm using the FPC connector 204, so that the fingers can be connected to the palm without additional wiring or soldering. The FPC connector can also be thinner because the flex circuit is thinner than wire connectors. The FCB can have a section of extra length 404, and the extra length section 404 can make assembly quicker and easier as it provides slack in the system between the finger and the palm. The extra length section allows slack in the system so that the connector 204 can be connected to the palm FCB 1002 easily. The extra length section 404 can also provide additional slack as the finger moves relative to the palm.
[0075] Strain relief loops 246 and 244 are shown in position as they are wrapped around a loop-holder (not shown) within the finger, and knot 242 is shown as it would be tied around a component within the finger, such as a linkage bar, (not shown) to hold the FCB in place while the finger is moving and bending. The loop holders and knot holder are described in more detail in later figures. Circuit unit 200, including FCB 202, is shown in the folded conformation as it would be threaded through the finger, including through the finger joints, with rotational encoders in the correct locations at joints, and force sensors in the correct locations within the finger, although the rest of the finger is not shown in Fig. 4A.
[0076] Fig. 4B is a detailed view of the pressure sensors shown in detail area 4B of Fig. 4A, according to an illustrative embodiment. Force sensor 226 includes electrodes 316 and 326 that are folded at hinge 336, and double sided dielectric adhesive 266 holding the electrodes near each other but slightly separated. As pressure is applied to electrode 316, the double sided dielectric adhesive 266 is slightly compressed, which results in a change in capacitance that can be measured by IC 270 and converted to a digital signal that can be transmitted through the FCB 202 to a processor that can be outside of the finger.
[0077] Fig. 4C is a cross sectional view of the sensors shown in Fig. 4A, taken along cross section line 4C-4C of Fig. 4A, according to an illustrative embodiment. The pressure sensors 222, 224, 226, and 228 can be connected through the FCB 202 to the IC 270, and IC 270 can be nestled within the finger tip cavity where space is less important and where the touch sensor IC 270 can be located close to the pressure sensors.
[0078] The sensor arrangement can be shielded with a conductive foil, such as aluminum foil, to shield the sensors from the external capacitance that can occur when bringing the sensor close to a conductive surface, such as a human finger or other conductive surface. Eliminating external capacitance allows for measuring the force acting on the sensors without having stray capacitance from electrically conductive surfaces nearby decrease the accuracy of the force measurements. The result is a very accurate sensor array that is also compact and low cost. In various embodiments, the sensors can be finalized with a protective cover made of a flexible plastic material. The protective cover for a finger can be a flexible or semi-flexible material around a conductive foil, while other force sensors in the palm of the hand can have a protective hard plastic cover, explained more fully below. In various embodiments, sensors can be covered with a hard plastic shell.
[0079] Fig. 5A is a bottom perspective view of a finger, according to an illustrative embodiment. and Fig. 5D is a bottom perspective view of various components inside of the finger of Fig. 5A, including structural components, and showing the placements of magnets for rotational sensors, according to an illustrative embodiment. Figs. 5A shows the finger 100 with a plastic covering over the fingertip, protecting the force sensors. Finger 100 can have a knuckle 112 between distal phalange 102 and middle phalange 104, and knuckle 112 can have an axis of rotation A. Similarly, knuckle 114 between middle phalange 104 and proximal phalange 106 can have an axis of rotation B, and knuckle 116. In various embodiments, there can be two joints between proximal phalange 106 and base 108, and curling joint 116 can have axis of rotation C, and yaw joint 118 can have axis of rotation D. In various embodiments, axis of rotation C and axis of rotation D can be 90 degrees from each other. In various embodiments, a universal joint can be used for knuckle 116 and joint 118, and axis of rotation C and axis of rotation D can be arranged in the same plane. Various arrangements of joints and axis are possible.
[0080] Fig. 5B is a side view of the finger of Fig. 5A, shown without the outer shell, according to an illustrative embodiment, and Fig. 5C is a cross section of the finger of Fig. 5B, taken along cross section line 5C-5C, and viewed from below, according to an illustrative embodiment. One or more of the phalanges can have multiple structural frame components inside a phalange. Distal phalange 102 can have a right frame 502 and a left frame 512. Terms like “left” and “right” are used herein to describe various components of a finger as a way to make the descriptions clear and easy to understand, however, it should be clear that features described as left can be on the right, and visa versa. Right frame 502 and left frame 512 can come together to form a distal bone 522. Structural components inside the finger can be referred to herein as bones, although it should be clear that the bones and joints in the finger 100 are not to be confused with the bones and joints of human anatomy, and can differ in number, shape, and arrangement from the bones of human anatomy.
[0081] The pressure sensors of the finger can be arranged around the exterior of the distal bone 522, so that the inner electrodes 312, 314, 316, 318 are held against the distal bone 522. When an object presses against the outer electrode 322, 324, 326, or 328, the force compresses the dielectric double sided adhesive material 262, 264, 266, or 268 within the sensor, resulting in a change in capacitance. The FCB can pass through the hollow inside of the distal bone 522 on the way to the middle bone 524.
[0082] Middle phalange 104 can have a right frame 504 and a left frame 514, and the right frame 504 and left frame 514 can come together to form a middle bone 524. Proximal phalange 106 can have a right frame 506 and a left frame 516, and the right frame and the left frame can come together to form a proximal bone 526. Base 108 can have an upper frame 508 and a lower frame 518, and the upper frame and the lower frame can come together to form a base bone 528. Terms like “upper” and “lower” are used herein to describe various components of a finger as a way to make the descriptions clear and easy to understand, however, it should be clear that features described as upper can be on the lower, and visa versa. An auxiliary bone 527 can be positioned between joint 116 and 118. This auxiliary bone 227 connects the joint 116 and joint 118, and together, the joint 116, auxiliary bone 527, and joint 118 allow the base 108 and proximal phalange 106 to move in multiple degrees of freedom relative to each other. Various bones can have hollow portions or hollow channels that can contain components of joints, magnets, sensors, FCB, and/or other components. A left frame and a right frame (or an upper frame and a lower frame) can be joined together to form a bone with various components held in place within the bone.
[0083] Fig. 5D is a bottom perspective view of various components inside of the finger of Fig. 5A, including structural components, and showing the placements of magnets for rotational sensors, according to an illustrative embodiment. Diametrically magnetized magnet 232, 234, 236, and 238 can be on-axis for each joint. The central axis of the disc-shaped magnet can be the same axis as the pivoting axis for the joint. As shown on magnet 238, this means that the N and S poles of the magnet can be on the flat surface of the magnet, with the N on one side and the S on the other side of the axis D. The specific rotation of the N and S around the axis can vary from that shown in Fig. 5D, however, the N and S can both be on the face and on opposite sides of the axis so that a diameter line connecting the N and the S passes through the central axis D. Each of the joints 112, 114, 116, and 118 can have a diametrically magnetized magnet arranged on-axis in the same way.
[0084] A finger 100 can have a linkage bar 530 that can link between bones. Linkage bar 510 can be anchored to the distal bone 502 at pivot 532, and linkage bar 510 can be anchored to proximal bone 506 at pivot 536. Distal bone 522, linkage bar 530, middle bone 524, and proximal bone 526 together can form a four-bar linkage, explained more fully below. Middle bone 524 can have a bar cavity 534 that can accommodate the linkage bar in different positions and orientations as the finger bends and straightens.
[0085] Fig. 5E is a detailed view of the area of detail 5E in Fig. 5C, showing an arrangement of joint components within the bone, according to an illustrative embodiment. Turning now to Figs. 5A, 5B, 5C, 5D, and 5E, the arrangement of a magnet, a rotational encoder, and the rotational axis of a joint are described. Joint 114 can have bearings 544 that facilitate the movement between middle bone 524 and proximal bone 526, and magnet 234 can be on-axis with the bearing and joint. Magnet 234 can secured to the middle bone 524, and the rotational position encoder 214 can be next to the magnet 234, but secured to the proximal bone 526. When the middle phalange 104 pivots relative to proximal phalange 106 around joint 114, the magnet 234 secured to the middle bone 524 pivots relative to the rotational encoder 214 secured to the proximal bone 526. As the magnet rotates relative to the rotational encoder, the N and S poles of the magnet rotate relative to the encoder, the encoder can sense the rotation of the magnet as the N and S poles travel around the axis. An air gap 556 can separate the magnet and sensor chip of the rotational encoder allowing them to rotate freely relative to each other without contacting each other. In various embodiments, the air gap 556 can be approximately 0.5 mm.
[0086] As shown in Figs. 5C and 5E, the rotational encoder chip 214 is mounted to the right proximal frame 516, and the magnet is mounted to the right middle frame 514, however, it should be clear that in various embodiments, the rotational encoder chip could be mounted to the left proximal frame 526 with the magnet on the left middle frame 524, and in various embodiments, the magnet could be on a proximal frame with the encoder on a middle frame. The arrangement of the magnet on one phalange with the encoder on the other phalange allows the encoder to detect the rotational position of the magnet, and thereby detect the rotational position of one phalange relative to the other. The specific arrangement between phalanges and between sides could be varied while still sensing the rotational position of one phalange relative to the other.
[0087] Each joint can have a similar arrangement of bearings, magnet, encoder, and air gap. Joint 112 can have bearings 542 that can be press fit into the frame allowing for free rotation between distal bone 522 and middle bone 524. Magnet 232 can be on axis along axis A with encoder 212 positioned near magnet 232 with an air gap 552 between the encoder and magnet that can be approximately 0.5 mm. As the distal bone and the middle bone move relative to each other around joint 212, the magnet rotates relative to the rotational encoder, and the rotational encoder can sense the changing position of the N and S poles. The sensed data of the magnet rotating relative to the encoder can then be used to determine the rotational position of the joint, and thereby the rotational position of the distal phalange relative to the middle phalange.
[0088] Similarly, joint 116 can have bearings 546, a magnet 236 that can be on-axis along axis C, and a rotational encoder 216 that can be positioned near the magnet 236 with an air gap 556 between the magnet and sensor that can be approximately 0.5 mm. Joint 118 can have bearings that can be on axis along axis D, and a rotational encoder 218 that can be positioned near the magnet 238 with an air gap between the magnet and encoder that can be approximately 0.5 mm. The sensed data of the magnet rotating relative to the encoder can then be used to determine the rotational position of the joint. The stack including the reference magnet, the air gap, the rotational encoder, and the FCB can be 9mm or less, resulting in a highly accurate sensor for measuring the position of the joint while also taking up very little space inside the knuckle and allowing for other components such as tendons to pass through the knuckle without interference.
[0089] In various embodiments, the rotational position sensors can be rotational potentiometers instead of contactless potentiometers. A rotational potentiometer can be free of magnets, and can include a shaft instead of a diametrically magnetized magnet. The rotational potentiometer can be an IC on the FCB, similar to the rotational encoders shown in Fig. 5D.The shaft can be press-fit into one side of a joint, such as a middle bone, and the rotational potentiometer can be mounted the other joint component, such as a proximal bone. The two parts of the joint that rotate relative to each other could then be connected by the shaft of the rotational potentiometer. However, this design that replaces the contactless potentiometer with a rotational potentiometer is superior to the potentiometer, at least because the potentiometer uses internal conductive brushes in an arrangement with friction that results in wear over time and eventual breakdown with repeated usage, while the magnet-based design has no friction and no wear, and because the potentiometer is susceptible to water while the IC of the contactless pentiometer can be sealed for a water resistant design. Accordingly, this novel design has implemented the use of a Hall effect magnet rotational position sensor that results in superior performance, superior lifespan, superior reliability, superior accuracy, and a superior compact design.
[0090] The innovative design described herein allows for a significant reduction in the space requirements of various components. By having a single FCB 202 that carries all signals through the finger in a compact arrangement, additional space is available to have rotational position sensors actually located on axis within each joint. And the compact design of the rotational position sensors allows enough space for the FCB to pass through the interiors of joints. Allowing the FCB to pass through the interior of a joint means the FCB is flexed less and requires less available slack along the FCB. Inferior prior art designs have been forced to route wires along the outside of a joint in a way that requires significant extra slack and results in significant wear on the wires.
[0091] In an embodiment, space requirements can be further minimized by having the rotational encoders 214 and 216 mounted along the inside of the proximal frame, with the FCB 202 routed along the edge and folded into the middle of the proximal bone. The FCB can be folded into the shape shown in Figs. 2A and 2B, with the encoders along the edge of the interior of the finger. The FCB can have a proximal segment 276, as shown in Fig. 2A, that can be pressed along the side of the proximal frame, and the FCB can be folded through three dimensions in space so that the FCB can pass through the middle of each joint and flex as the joints move. The FCB 202 can be tied in a knot 242 around the linkage bar 530 so that the FCB remains in position arranged down the centers of joints 112 and 114. The split 252 in the FCB allows the FCB to flex more easily as it passes down the centers of joints 116 and 118, and as the joints 116 and 118 rotate along different axis and the phalanges move in multiple different directions relative to each other.
[0092] A multifunctional clip 564 can hold encoder 214 in place on the proximal bone 526, while also providing a loop-holder to hold strain relief loop 244. Fig. 6A is an exploded bottom perspective view of various components inside the finger of Fig. 5A, including multipurpose clips that can maintain the positions of rotational encoders and the FCB; according to an illustrative embodiment, and Fig. 6B is a side view of various components inside the finger of Fig. 5A, showing rotational encoders held in place by the clips and showing the arrangement of the FCB and magnets; according to an illustrative embodiment. In Fig. 6A, the multifunctional clip 564 is shown isolated in position 564A before assembly, and is shown in assembled position 564B where it can hold the rotational position encoder 214 in place. Turning to Figs. 5C, 5E, 6A, and 6B, the multifunctional clip 564 can hold encoder 214 and multifunctional clip 566 can hold encoder 216 in place on the proximal frame. Together, clips 564 and 566 secure the proximal segment 276 in place along the proximal frame. The clips hold the FCB in place while also securing the encoder precisely on the axis of rotation. The clips also contribute to keeping the sensor and the magnet slightly separated by an air gap, which allows for improved operation of the rotational position sensor.
[0093] Strain relief loop 244 is wrapped around loop holder 604 of clip 654, and strain relief loop 246 is wrapped around loop holder 606 of clip 566. Loop holders 604 and 606 can work together to support the FCB 202 in place down the middle of the finger. Strain relief loops 244 and 246 can also be seen in Fig. 4A. Having the FCB wrapped around the loop holders with strain relief loops not only keeps the FCB in place, but the strain relief loops can provide slack when necessary and hold excess slack out of the way when necessary as the finger bends and straightens. Similarly, clip 562 helps to secure a rotational encoder precisely on axis for joint 112, and the FCB holder 602 of clip 562 helps to route the FCB 202 in place down the middle of the finger.
[0094] Rotational position encoders 212 and 214 can work together to sense force on the surface 570 of distal phalange 102, as indicated in Fig. 5A. Capacitive force sensors can sense contact force on pressure sensitive areas 122, 124, 126, and 128, however, the bottom surface of the finger, shown as 570 in Fig. 5A, may not need a capacitive force sensor. A four-bar linkage system within the finger can work with the rotational position encoders 212 and 214 to sense force on surface 570. Capacitive force sensors can be shielded by a thin layer of aluminum foil. As shown in Fig. 6B, the foil 610 can shield each of the sensors. The protective outer cover of the fingertip can then be applied over and around the foil.
[0095] Fig. 7A is a schematic diagram of a 4-bar linkage system that can use magnetic rotational sensors to determine torque and pressure, shown with the finger in a straight conformation, according to an illustrative embodiment. In this schematic diagram, distal segment 702 is joined to middle segment 704 at joint 712, and middle segment 704 is joined to proximal segment 706 and joint 714. Distal segment 702 also has a pivot 722 that is connected to linkage bar 720, and linkage bar 720 is connected to proximal segment 706 at pivot 726. Distal segment 702, middle segment 704, and proximal segment 706 can be rigid. Linkage bar 720 can be made from a semi-rigid material, so that linkage bar 720 will flex under force. Joint 714 can be an active joint driven by a motor such as a servo located within the palm or arm of a robot that can be connected to the joint with tendons, explained more fully below. When the motor forces the joint 714 to rotate, or put another way, when the motor forces the middle segment 704 to move around the joint 714 relative to the proximal segment 706, the linkage bar between pivot 726 and pivot 722 will pull the distal segment 702 to move around the joint 712 relative to the middle segment.
[0096] Fig. 7B is a schematic diagram of the 4-bar linkage system of Fig. 7A, shown with the finger in a bent conformation and without applied pressure, according to an illustrative embodiment. After the motor has forced the joint 714 to rotate, or put another way, after the motor has forced the middle segment 704 to move around the joint 714 relative to the proximal segment 706, the linkage bar 726 between pivot 726 and pivot 722 has now pulled the distal segment to move around joint 712 relative to the middle segment. The four-bar linkage system causes both joints to rotate, or causes all three segments to move around the joints, while only one of the joints is directly powered. This four-bar linkage system allows the finger to curl around multiple joints without the need to provide a motor to power movement at each joint. The angle of the passive joint 712 can be computed from the angle of the driven joint 714 and the lengths of the segments.
[0097] Fig. 7C is a schematic diagram of the 4-bar linkage system of Fig. 7B, shown with pressure applied to an outer, fingernail side of a finger, thereby flexing the linkage bar in a shortened conformation; according to an illustrative embodiment. When force is applied to the top, fingernail portion of the distal segment 702, such as in the direction of arrow T, the semi-rigid linkage bar 720 can compress or otherwise flex to allow the distal segment 702 to rotate around the passive joint 712 under the pressure in the direction of arrow U. The system can then calculate the torque applied to the fingernail area by measuring the rotational angle of joint 712 and the rotational angle of joint 714 and comparing them to the no-load condition shown in Fig. 7B.
[0098] Fig. 7D is a schematic diagram of the 4-bar linkage system of Fig. 7B, shown with pressure applied to an inner side of a finger, thereby flexing the flex bar in an elongated conformation; according to an illustrative embodiment. When force is applied to the bottom of the finger, such as in the direction of arrow V, the semi-rigid linkage bar 720 can stretch or otherwise flex to allow the distal segment 702 to rotate around the passive joint 712 under the pressure in the direction of arrow W. The system can then calculate the torque applied to the bottom of the finger by measuring the rotational angle of joint 712 and the rotational angle of joint 714 and comparing them to the no-load condition shown in Fig. 7B.
[0099] Fig. 8A is a perspective view of the interior of the robotic finger of Fig. 8A showing the components of the 4-bar linkage system, according to an illustrative embodiment, Fig. 8B is a top view of the partial robotic finger shown in Fig. 8A, according to an illustrative embodiment, and Fig. 8C is a cross section view of the partial robotic finger of Fig. 8B, taken along cross section line 8C-8C, according to an illustrative embodiment. Distal bone 522 can be distal segment 802 of the four-bar linkage system, middle bone 524 can be middle segment 804 of the four bar linkage system, and proximal bone 526 can be proximal segment 806 of the four bar linkage system. Distal segment 802 is connected to middle segment 804 at joint 112, and proximal segment 806 is connected to middle segment 804 at joint 114. Linkage bar 530 can link between proximal segment 806 and distal segment 802. Linkage bar 530 can be anchored to proximal segment 806 at pivot 536, and anchored to distal segment 802 at pivot 532. Middle bone 524 can have a bar cavity 534 that can accommodate the semi-rigid linkage bar 530 in different positions and orientations as the finger bends and straightens.
[00100] This arrangement creates a four-bar linkage system with a known relationship between the two rotational joints 112 and 114. In various embodiments, the linkage bar 530 can have an S-curve, or other shape, along the length of the bar that allows it to flex in either direction as force is applied to the top or bottom of the finger. By measuring the rotational position of joint 112 and joint 114, the system can calculate force being applied to the distal segment that causes the linkage bar 530 to flex one way or the other.
[00101] Fig. 8D is a cross section view of the partial robotic finger of Fig. 8B, taken along cross section line 8C-8C showing the finger in a bent conformation, according to an illustrative embodiment. Turning to Figs. 8C and 8D, flexor tendon 822 can pull on the middle segment 804 to cause the middle segment 804 to rotate around the joint 114 into a bent conformation, as shown in Fig. 8D. Extensor tendon 824 can pull on the middle segment 804 to cause the middle segment 804 to rotate around the joint 114 into a straight conformation, as shown in Fig. 8C. When the flexor tendon 822 powers segments 804 and 806 into a bent conformation around joint 114, the linkage bar 530 pulls segment 802 into a bent conformation around joint 112, as shown in Fig. 8D. When the extensor tendon 824 powers the segments 804 and 806 into a straight conformation around joint 114, the linkage bar 530 pulls segment 802 into a straight conformation around joint 112, as shown in Fig. 8C. The two tendons 822 and 824 can pass through the center of joint 116 as a tendon bundle 820. However, it should be clear that the tendons are not required to be bundled together as a tendon bundle 820 to pass through the finger, the palm, or the wrist. Because of the various innovative and space saving designs described herein, more space is available inside the fingers, palm, and wrist than is required for the various components.
[00102] Fig. 9 is a perspective view of an assembled robotic hand, including a wrist, palm, and fingers, according to an illustrative embodiment. Robotic hand 900 can have a plurality of fingers 100 that can be attached to a palm 910. Tendons and FCBs from each finger can pass through the palm and through the wrist 920 to connect to various circuits, processors, servos, etc. of a robot. In various embodiments, a robotic hand can have five fingers, more than five fingers, or less than five fingers. As used herein, the word “palm” refers to the portion of a hand that does not include fingers. The word “palm” is not intended to refer to a particular side of the hand.
[00103] Fig. 10 is a perspective view of the circuitry, including sensors, from inside the robotic hand with fingers, according to an illustrative embodiment. Palm circuitry 1000 can include a palm FCB 1002, palm force sensors 1022, 1024, 1026, and 1028, finger rotational position encoders 1012 and 1014, and wrist rotational position encoders 1016 and 1018. Palm circuitry 1000 can include one or more FPC connectors 1004 that allow finger circuitry units 200 to be connected to the palm circuitry unit 1000.
[00104] Each finger circuit unit 200 can be plugged into an FPC 1004 on the palm. The FCB of the palm can have traces that correspond to the traces of the finger FCBs 202. All of the electrical signals originating from within a finger, such as sensed data from force sensors and/or rotational position sensors of a finger, can be transmitted through the FCB of the finger, and then transmitted to the FCB of the palm. The signals from more than one finger can then be transmitted through the FCB of the palm back to the arm. In this way, there is no need for bulky wires or a large number of wiring connections within the palm. Each finger can be connected to the palm FPC 1004, and then all sensed information can be transmitted to the arm through the palm FCB, thereby substantially reducing the space requirements within the palm.
[00105] Fig. 11A is a perspective view of the palm circuitry, including sensors, from inside of a robotic palm shown without fingers, according to an illustrative embodiment, and Fig 11B is a top view of the circuitry of Fig. 11A, shown in a flat conformation before the sensors are folded and before the FCB is arranged into the shaped used inside the palm of Fig. 9, according to an illustrative embodiment. Palm circuitry 1002 can be manufactured flat as a single sheet to reduce costs, and then it can be folded into the appropriate conformation.
[00106] Palm circuitry 1002 can include two force sensors 1022 and 1024 that are arranged on the top of the palm portion to sense contact force on the back of the hand, and two force sensors 1026 and 1028 that are arranged on the bottom of the palm portion to sense contact force on the bottom, or inside of the hand. These palm force sensors can be constructed in the same way as the force sensors in the fingers. As shown in Figs. 11A and 11B, capacitive force sensor 1022 can include electrode 1112 and electrode 1122. Electrode 1112 and electrode 1122 can be folded at hinge 1132, and the two electrodes can be brought together and stuck together using a dielectric double sided adhesive 1162. The descriptions of the manufacturing and functionality of the capacitive force sensors of the fingers, described above, also describes the manufacturing and functionality of these capacitive force sensors in the palm. Sensors 1022, 1024, 1026, and 1028 can be manufactured flat and folded together with dielectric double-sided adhesive separating the two electrodes. Sensor 1024 includes electrodes 1114 and 1124 separated by hinge section 1134, and dielectric double sided adhesive 1164. Sensor 1026 includes electrodes 1116 and 1126 separated by hinge section 1136, and dielectric double sided adhesive 1166. Sensor 1028 includes electrodes 1118 and 1128 separated by hinge section 1138, and dielectric double-sided adhesive.
[00107] Rotational position encoders 1016 and 1018 can work with diametrically magnetized magnets to sense the rotational position of the wrist in two directions including an up-down direction and a side-to-side, or yaw, direction. The outer fingers, which can be referred to as a pinkie and a thumb, can have an additional joint, described more fully below, that allows the base of the finger to pivot relative to the rest of the palm. Rotational position encoder 1012 can work with a diametrically magnetized magnet to sense the rotational position of the base joint for the pinkie. Rotational position encoder 1014 can work with a diametrically magnetized magnet to sense the rotational position of the base joint for the thumb. The descriptions of the manufacturing and functionality of the rotational position sensors of the finger joints, described above, also describes the manufacturing and functionality of these rotational position sensors in the palm.
[00108] In various embodiments, the palm FCB 1002 and/or finger FCB can include ancillary circuitry such as ancillary circuitry 1172 and 1174. In various embodiments, ancillary circuitry 1172 and or 1174can be multiplexing ICs that can help to connect the multiple sensors to a single data line. This can reduce the number of traces required on the FCB, and can therefore reduce the size of the FCB as it passes through various space-limited components such as the wrist. In various embodiments, there can be a processor and an Inertial Measurement Unit (IMU). Space savings from various features herein, including integrated sensors, allow for placement of additional components such as processor units, multiplexing ICs, inertial measurement units, temperature sensors, etc. on the FCB and within the hand. Ancillary circuitry 1172 and/or 1174 can be various multiplexing ICs, processors, IMUs, and/or various other ancillary circuitry.
[00109] As shown in Fig 11B, pinkie circuit 1142 and thumb circuit 1144 of the palm FCB 1002 can be manufactured in the same way as each other, with the circuits manufactured as components of a symmetric FCB 1002. The FCB pinkie circuit 1142 and thumb circuit 1144 can be folded into different conformations, so that the thumb circuit can be positioned further back along the side of the palm. This allows for an opposable thumb to be positioned back from the other fingers while also allowing the circuitry to be easily manufactured symmetrically. This symmetrical manufacturing eliminates the need for separate FCBs to be produced for left hands vs right hands, which further reduces manufacturing costs.
[00110] The FCB 1002 can be folded in a way that includes strain relief loops 1152 and 1154 that can allow the FCB to flex and move as the hand moves relative to the wrist. Folding sections 1151 and 1153 can be folded to create strain relief loops 1152 and 1154, respectively. The FCB can also be folded in a way that includes folded sections 1056 and 1058 at the bottom, near the fingers. These folded loops 1056 and 1058 can allow the FCB to elongate during assembly, including during attachment of the fingers, and then allow the FCB to be tucked into a compact design after assembly. Folding sections 1155 and 1157 can be folded to create folded loops 1156 and 1158, respectively.
[00111] The FCB 1002 can be manufactured with a tendon hole 1176 for the tendons of each hand. The tendons, which can be arranged as a tendon bundle, can pass through the tendon hole 1176 and can connect with servo motors in the arm. By having a hole for the tendons to pass through the FCB, the FCB and the tendons can occupy the same areas of the hand without interfering with each other.
[00112] Fig. 12A is an exploded perspective view of the top of a partially assembled palm, showing circuits, sensors, and removed back cover, according to an illustrative embodiment. The circuitry unit 1002 of the palm can be joined with a rigid plastic palm bone 1202. In various embodiments, the palm bone can include multiple frame components that can be assembled with the circuitry unit 1002, and/or the circuitry unit 1002 can be folded into the folded conformation of Fig. 11A with the palm bone. Capacitive force sensors can be arranged on the exterior of the palm bone. In various embodiments, the sensors can be finalized with a protective cover made of a flexible plastic material. In various embodiments, sensors can be covered with a hard plastic shell that can be suspended on pegs above the sensors. These pegs can increase the distance to the external contact surface, thereby minimizing external capacitance and minimizing interference with the measurement of force that is measured by measuring the capacitance between the two electrodes.
[00113] A rigid or semi-rigid top cover 1204 can snap into engagement with the palm bone 1202. The top cover 1204 can have pegs 1222 and 1224 that can align with the sensors on the top of the hand 1022 and 1024. In a fully assembled position, the pegs 1222 and 1224 can rest against the top sensors 1022 and 1024. The top sensors can thereby be sandwiched between the pegs of the top cover and the palm bone. When an object is pressed against the top cover 1204, the forces are transmitted through the pegs to the sensors on the top of the hand, and the sensors 1022 and 1024 are thereby squeezed between the pegs and the palm bone. As the capacitive force sensors 1022 and 1024 are squeezed, the capacitance between the two electrodes changes, and the quantity of force can be determined from the change in capacitance.
[00114] Fig. 12B is an exploded perspective view of a partially assembled palm, showing circuits, sensors, and removed hand bottom cover, according to an illustrative embodiment. Similar to the top of the palm shown in Fig. 12A, the bottom of the palm has force sensors 1026 and 1028 that can be on the surface of the palm bone 1202. A rigid or semi rigid bottom cover 1206 can snap into engagement with the palm bone 1202. The bottom cover can have sensor engagement points 1226 and 1228 that can align with the sensors 1026 and 1028 on the bottom of the hand. The bottom sensors can thereby be sandwiched between the palm bone and the bottom cover 1206. When an object is pressed against the bottom cover 1206, the forces are transmitted through the bottom cover to the sensors on the bottom of the hand, and the sensors 1026 and 1028 are thereby squeezed between the bottom cover and the palm bone. As the capacitive force sensors 1026 and 1028 are squeezed, the capacitance between the two electrodes changes, and the quantity of force can be determined from the change in capacitance. The capacitive force sensors in the palm operate under the same principles as the capacitive force sensors in the fingers, and similarly, they occupy very little space, are manufactured as a single component with the FCB, are very cheap to manufacture, and do not require additional wires or connections inside the hand.
[00115] As shown in Figs. 12A and 12B, the symmetrical circuitry unit 1202 can be folded with the pinkie in a first conformation and the thumb folded in a second conformation, resulting in an asymmetrical hand with an opposable thumb. Fig. 13A is a partially assembled view of a hand, showing thumb and pinkie joints and thumb and pinkie joint rotational position sensors, according to an illustrative embodiment. Thumb 1302 is positioned further back on the hand, closer to the wrist 1400. In addition to the various finger joints described above, thumb 1302 and pinkie 1304 have an additional joint that allows them to pivot inward in a direction that is into the page, when looking at Fig. 13A. That is to say, pinkie 1304 and thumb 1302 can be bent inward towards the bottom of the hand in a direction that allows the opposable thumb to help to grip objects in conjunction with other fingers. The pinkie 1304 can also pivot inwards towards the bottom of the hand in a direction that allows the pinkie 1304 to help grip objects in conjunction with other fingers. A pair of bevel gears can be used to translate the movement of tendons to the inward pivoting of the pinkie and thumb.
[00116] Fig. 13B is a detailed view of a pinkie joint 1320 of Fig. 13A, showing an arrangement of bevel gears, according to an illustrative embodiment. The top bevel gear 1340 can have a tendon track 1342 that accommodates a tendon that can connect to a servo in the arm. Top bevel gear 1340 also has gear teeth 1344 that engage with gear teeth 1354 in the bottom bevel gear 1350. As the tendon rotates the top bevel gear, the movement of the tendon is translated to the bottom bevel gear, which then causes the base 108 of the pinkie 1320 to rotate around axis E. A hollow canal 1356 can extend through the joint 1320, and the hollow canal can allow the FCB and tendons of the finger to pass through the center of the joint. Similar to other joints, the hollow center of the joint allows the FCB to pass through the joint with minimal bending of the FCB as the finger is moving. The pinkie joint 1320 can be aligned behind the ring finger 1308 and directly in line with the ring finger 1308, so that the FCB and tendons of the ring finger can pass through the center of the pinkie joint 1320. The thumb joint 1310 can have similar construction, with a hollow canal, and can be aligned behind the index finger 1306 and directly in line with the index finger 1306, so that the FCB and tendons of the index finger can pass through the center of the thumb joint 1310.
[00117] A diametrically magnetized magnet 1360 can be embedded inside the top bevel gear 1340, and acts as a reference for the rotational encoder within the joint 1320. Fig. 13C is a detailed view of the pinkie joint of Fig. 13B, showing a rotational position sensor within the joint, according to an illustrative embodiment. Rotational position encoder 1012 can detect the rotational position of magnet 1360 within top bevel gear 1340. As the top bevel gear turns, and thereby turns the lower bevel gear and causes the pinkie base 108 to rotate around axis E, the rotational position encoder 1012 can detect the rotational movement of the diametrically magnetized reference magnet within the top bevel gear. In this way, the rotational position encoder 1012 is able to detect the rotational position of the joint 1320 while still allowing the center of the joint to remain hollow. Similarly, the thumb 1302 has a thumb joint 1310 that operates under the same principles, including a pair of bevel gears, and a rotational position encoder that detects the rotational position of a reference magnet embedded within a bevel gear.
[00118] 14A is a perspective view of the wrist of Fig. 9, showing the hollow central channel that can accommodate tendons and FCBs, according to an illustrative embodiment. Wrist 1400 can use a universal joint 1412 that can allow for side-to-side yaw movement around axis F, and up-and-down movement around axis G. A hollow central canal 1402 allows various tendons and FCB from the hand to pass through the center of the wrist, including passing through axis F and axis G. Allowing the FCB to pass through the center of the wrist reduces the strain on the FCB as the various joints are moving. An outer support structure 1404 can hold all of the various components within the wrist in place.
[00119] Fig. 14B is a perspective view of selected components within the palm of Fig. 12B and the wrist of Fig. 14A, showing bevel gear components, according to an illustrative embodiment. The universal joint 1412 can have a right side bevel gear 1422, a top bevel gear 1424, and a left bevel bear 1426. As used herein, the labels left, top, and right are used for clarity and simplicity of explanation, and are not intended to refer to any absolute direction. The right side bevel gear 1422 can have a tendon track 1428 and tendon attachment points 1430. Tendons can be routed around the track and connect between the attachment points 1430 and servos, so that the servo in a different location, such as the arm, can rotate the right side bevel gear 1422. Similarly, the left side bevel gear 1426 can have a tendon track and tendon attachment points, so that the left side bevel gear can also be powered by a servo in a different location, such as the arm. Tendons can pass through the central canal 1402 to connect to servos that can be located in the arm.
[00120] When both the left side bevel gear and the right side bevel gear are rotated in the same direction around axis G, the wrist rotates in that direction around axis G. When the left side bevel gear is rotated in a first direction around axis G, and the right side bevel gear is rotated in the opposite direction around axis G, the wrist rotates around axis F. The loops folded into the FCB at the wrist allow the wrist to bend in different directions without pulling on or causing strain on the FCB.
[00121] Fig. 14C is an exploded view of the left bevel gear and outer structure of the wrist of Fig. 14B, showing a rotational position sensor; according to an illustrative embodiment. Turning to Figs. 14A, 14B, and 14C, the bevel gear 1426 can include a clip 1446 that holds the rotational position encoder 1018 in place on axis G. An insert 1448 can help to hold the rotational position encoder 1018 in the clip 1446. Diametrically magnetized magnet 1450 can be mounted in the side arms 1406 so that the rotational position encoder 1018 can sense the rotational position of the magnet 1450, and therefore sense the rotational position of the bevel gear 1426. The rotational position encoder 1018 and magnet 1450 form a rotational position sensor 1452 that is on axis with axis G.
[00122] Wrist 1400 can have two rotational position sensors located within any two of the three bevel gears. By sensing the rotational position of any two out of the three bevel gears, the processor can determine the rotational position of the universal joint around both the F axis and the G axis. In various embodiments, rotational position encoder 1016 and rotational position encoder 1018 can be on the left and right, or the left and top, or the top and right bevel gears. A rotational position sensor located within the top bevel gear can be on axis with axis F.
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

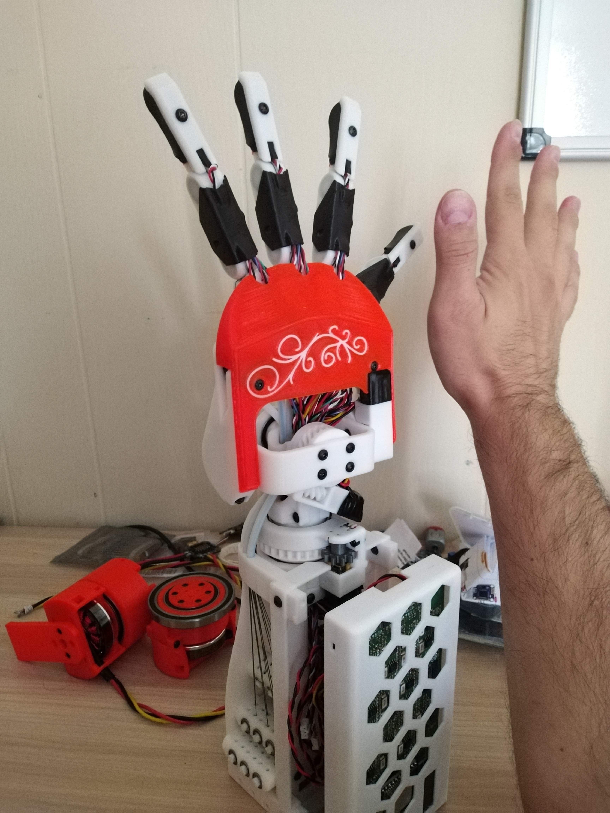
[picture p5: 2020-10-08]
media/mechahand_mk10_progress_top.jpg

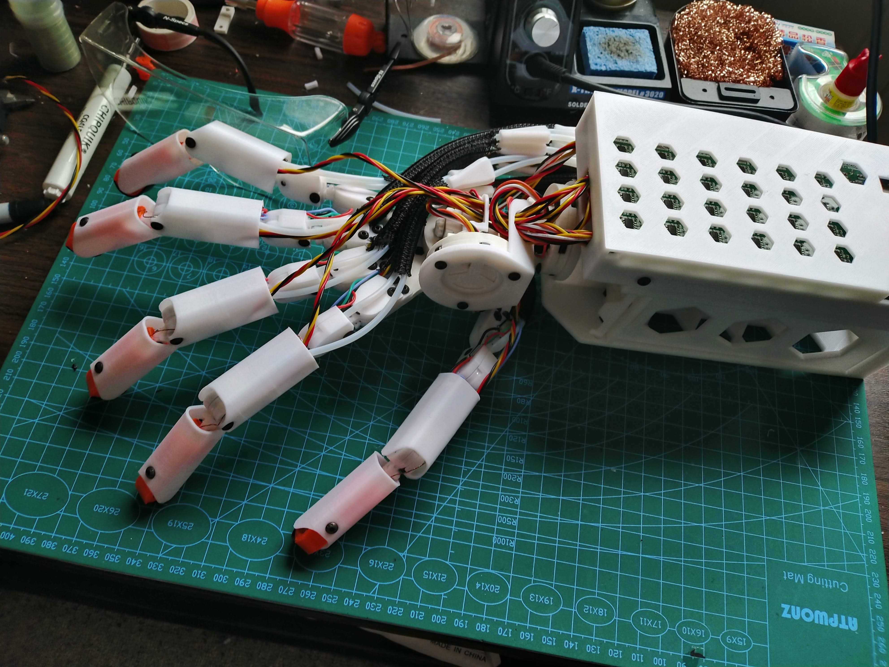
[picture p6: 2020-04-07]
media/mechahand_mk6.jpg

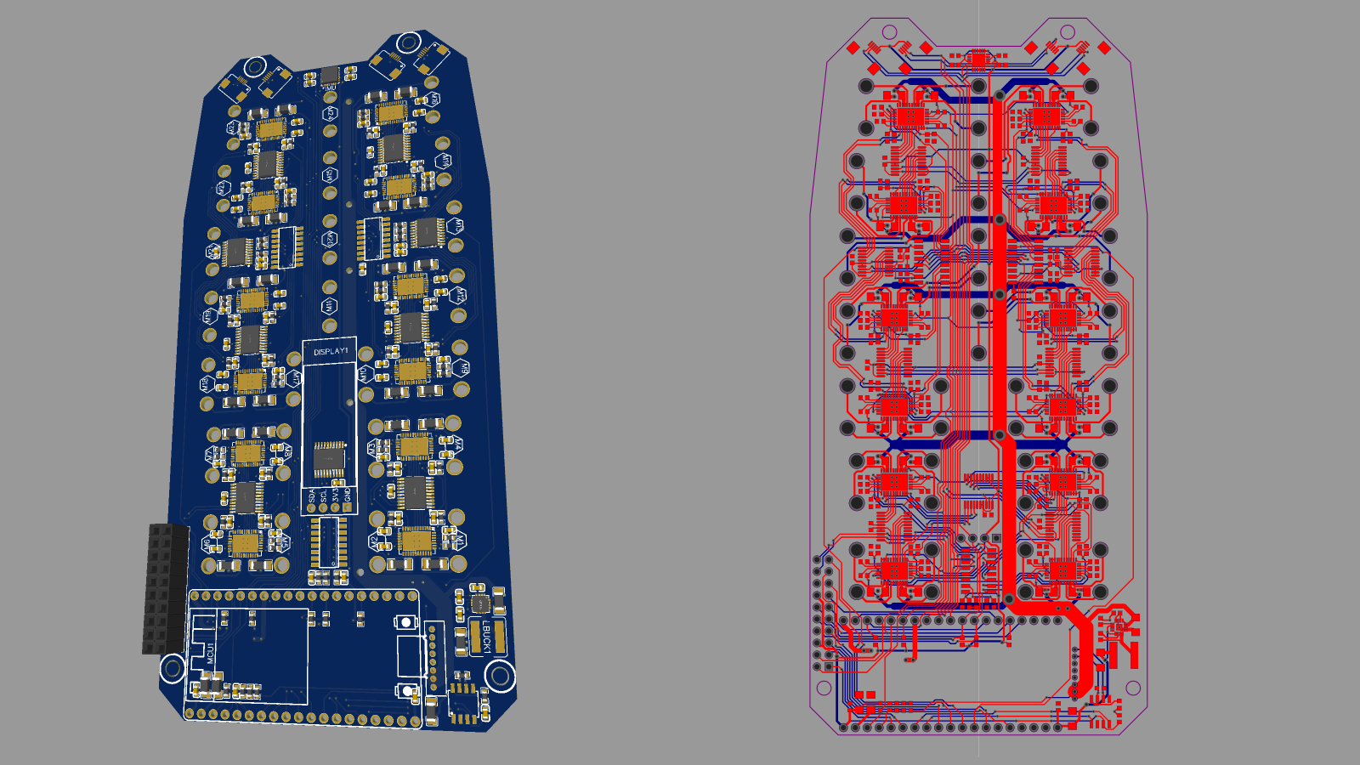
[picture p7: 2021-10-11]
media/mechahand-mk11-circuit-dev.png

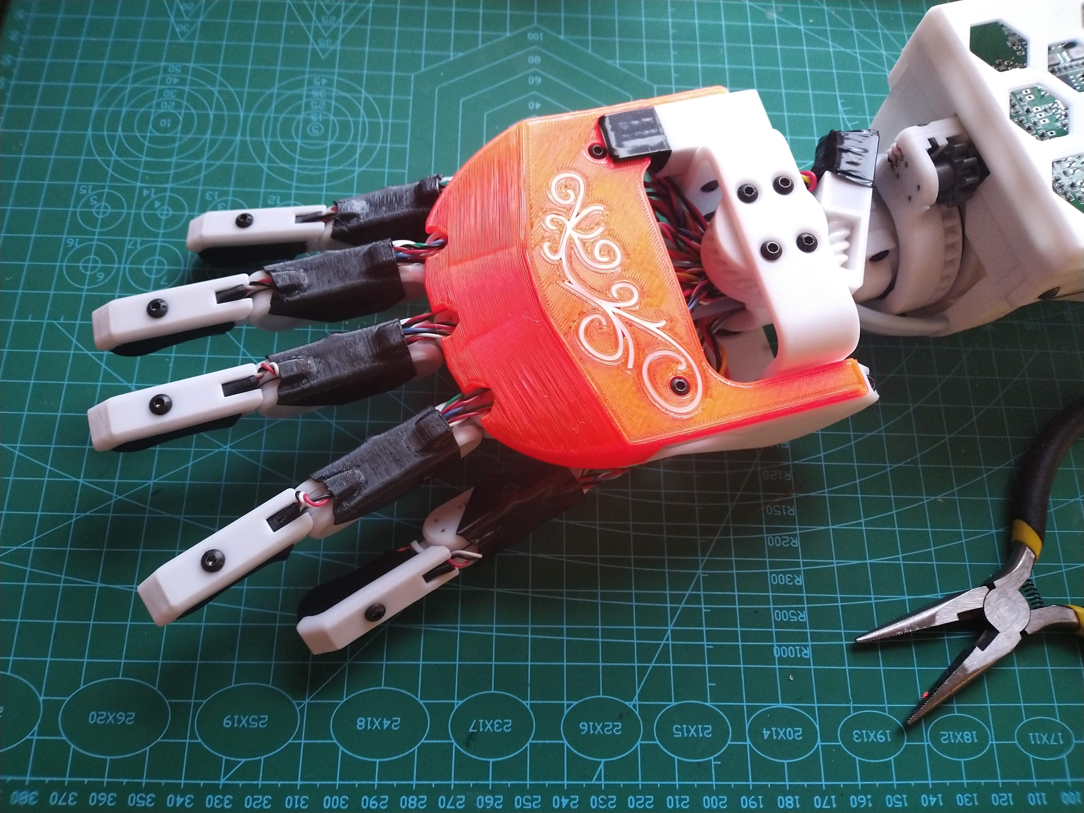
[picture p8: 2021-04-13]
media/mechahand_mk10_top_view.jpg

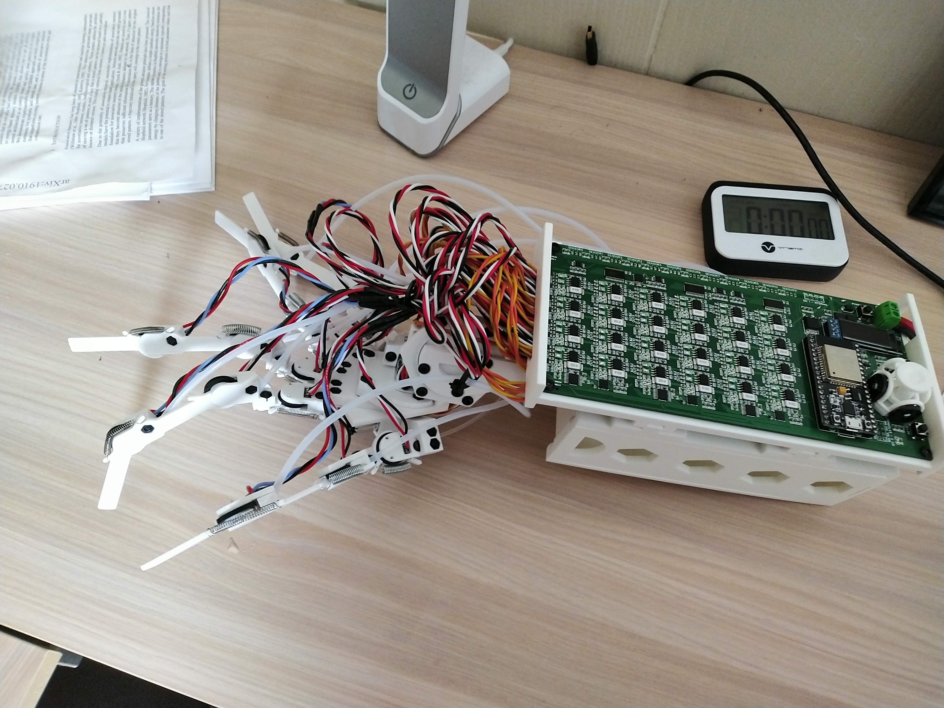
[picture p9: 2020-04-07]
media/mechahand_mk4.jpg

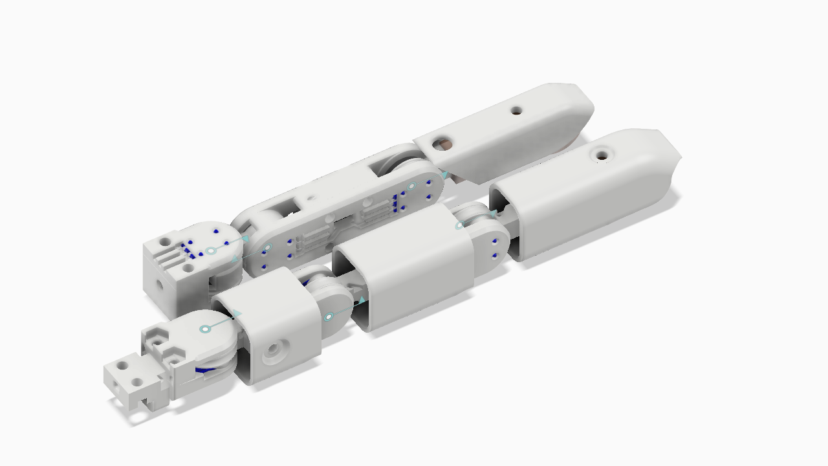
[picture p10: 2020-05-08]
media/mk_9_vs_mk_8_finger.png

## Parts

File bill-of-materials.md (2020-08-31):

Item                                   | Quantity | Batch quantity | Batch price | Unit price | Price $ | Notes                                                               | Link
---------------------------------------|----------|----------------|-------------|------------|---------|---------------------------------------------------------------------|--------
PLA filament 1kg                       | 0.6      | 1              | 25          | 25         | 15     | Determines color. PLA used for ease of printing finer details.       | https://www.amazon.com/gp/product/B07WDWZT87
PETG filament 1kg                      | 0.2      | 1              | 23          | 23         | 4.6     | PETG could be replaced with PLA or vice-versa.                      | https://www.amazon.com/gp/product/B07P2VVFXQ
TPU filament 1kg                       | 0.2      | 1              | 25          | 25         | 5       | Flexible, grippy filament needed for finger and palm covers.        | https://www.amazon.com/gp/product/B074DV9JMX
M3 hex nuts                            | many     | 150            | 7           | 0.05       | 7       | Need lots of nuts, this is only type used, expect to lose some.     | https://www.amazon.com/gp/product/B07H1NPJGP
M3 8mm hex socket button head screw    | many     | 100            | 8           | 0.08       | 8       | Main screw size used, need a bunch of these to screw around.        | https://www.amazon.com/gp/product/B01B1OD62C
M3 100pcs 20/25/30/35/40mm             | 0.2      | 1              | 12          | 12         | 2.2     | Need few larger bolts for the wrist assembly. Useful for arm too.   | https://www.amazon.com/gp/product/B076LMXW17
M3 250pcs 6/8/10/12/16mm               | 1        | 1              | 12          | 12         | 12      | Need varied sizes throughout hand design, but few of each size.     | https://www.amazon.com/gp/product/B0716Y5WZZ
6mm split rings double loop            | 40       | 200            | 5.6         | 0.03       | 1.1     | Need rings to tie and tension the finger tendons, expect loses.     | https://www.amazon.com/gp/product/B083JXLYK5
25 lb monofilament fishing line        | 0.2      | 1              | 7.5         | 7.5        | 1.5     | Monofilament important! Some tendons need to stretch. 20-30 lb ok.  | https://www.amazon.com/gp/product/B00ARHUIJ4
50 lb braided fishing lines            | 0.2      | 1              | 10          | 10         | 2       | Need strong, stiffer, thinner wire for tendons. Under 0.4 mm dia!   | https://www.amazon.com/gp/product/B01LYFMOBY
PTFE bowden tube 5ft 2mm ID x 4mm OD   | 0.5      | 1              | 7           | 3.5        | 3.5     | 2mm x 4mm is the most common, but also sweet spot for flex/stiff.   | https://www.amazon.com/gp/product/B073RDFTDV
Resistive strain gauge BF350-3AA       | 20       | 50             | 19          | 0.38       | 7.6     | Strictly need 12, but expect to damage some; or many on first try.  | https://www.amazon.com/gp/product/B07G42QW2S
GA12-N20 DC12V micro gear motor 100RPM | 22       | 22             | 57          | 2.59       | 57      | Might damage gears in some motors, get 2 spare.                     | https://www.aliexpress.com/item/4000274747864.html
RDC503051A Rotary position sensor 10K  | 20       | 40             | 40          | 1          | 20      | Much cheaper in large batches.                                      | https://www.mouser.com/ProductDetail/Alps-Alpine/RDC503051A?qs=j%252B1pi9TdxUY%2FAK%2Fo1fNF6g%3D%3D
6802-2RS deep groove ball bearings     | 4        | 8              | 8.8         | 1.1        | 4.4     | 2 extra could be used for the upper arm.                            | https://www.amazon.com/gp/product/B07FWGSFLN
6806-2RS deep groove ball bearings     | 2        | 10             | 14.2        | 1.4        | 2.8     | 4 extra could be used for the upper arm.                            | https://www.amazon.com/gp/product/B082PXK5K9
MR95ZZ 5x9x3 mm miniature bearings     | 20       | 20             | 7.1         | 0.36       | 7.1     | 1 spare in case it gets lost. Preferably more spares, these cheap.  | https://www.aliexpress.com/item/32824479804.html
MR128ZZ 8x12x3.5 mm miniature bearings | 5        | 10             | 3.9         | 0.39       | 2.0     | 1 spare in case it gets lost.                                       | https://www.aliexpress.com/item/4000324040769.html
2S 7.4V LiPo battery with deans plug   | 2        | 2              | 33          | 16.5       | 33      | 4S batteries should be better. Under 25V max, closer to 12V motors. | https://www.aliexpress.com/item/32995549798.html
T-Plug deans style 10cm wire           | 1        | 5              | 10          | 2          | 2       | If wiring 2 2S batteries in series, you can use 3x of these.        | https://www.amazon.com/T-Plug-T-Connectors-Deans-Style-BDHI-28/dp/B07MDGT5C1
6x6x5 mm tactile push button switches  | 1        | 1000           | 15          | 0.02       | 1       | Any common button should work. Plastic button might need adjusting. | https://www.aliexpress.com/item/32421383273.html
JST 2.0PH 3pin connector 30cm wires    | 20       | 50             | 8           | 0.16       | 3.2     |                                                                     | https://www.aliexpress.com/item/32958845278.html
JST 2.0PH 2pin connector 30cm wires    | 20       | 50             | 7           | 0.14       | 2.8     | 20cm can also work for close motors, but need extra custom cables.  | https://www.aliexpress.com/item/32958845278.html
30AWG stranded flexible silicone wire  | 0.3      | 1              | 1           | 15         | 5       | Need thin and flexible wires for fingers, 600cm total, multi color. | https://www.amazon.com/gp/product/B07G2SWB19
750 pcs 2.0mm JST-PHR connector kit    | 0.5      | 1              | 1           | 14         | 7       | Need female housing and crimp pins for wires. 26 3-pin, 20 2-pin.   | https://www.amazon.com/gp/product/B07D241T3M
2 pole screw terminal block 5mm pitch  | 1        | 20             | 6           | 0.3        | 1       |                                                                     | https://www.amazon.com/gp/product/B07NSKXGFQ
KeeYees 2.4GHz 2 core ESP32 WROOM-32   | 1        | 2              | 15          | 7.5        | 7.5     | Other dev kits might have slightly different pinouts!               | https://www.amazon.com/gp/product/B07QCP2451
LM2596 DC-DC buck converter 43x21mm    | 1        | 10             | 14          | 1.4        | 1       | Size must be within 1mm of 42x21mm. Linked is actually 43mm!        | https://www.amazon.com/gp/product/B07VVXF7YX
0.91 inch OLED I2C display SSD1306     | 1        | 2              | 8.6         | 4.3        | 4.3     |                                                                     | https://www.amazon.com/gp/product/B07FMDB6TR
2200uF 25V 13x21mm aluminium capacitor | 0        | 10             | 2.6         | 0.3        | 0       | Skip! Problem with start-up circuit will fry diode and weld button. | https://www.aliexpress.com/item/32885108458.html
24Drive PCB and SMT assembly by jlcpcb | 1        | 5              | 310         | 62         | 62      | Automatic assembly strongly recommended! Can order batch of 2.      | https://jlcpcb.com

Amortized total: $292 ($230 components + $62 pcb).

Single hand total: $603 ($413 component batches + $190 batch of 2 pcb).
Pair of hands total: $700 (2 batches of motors, more screws and bearings needed).

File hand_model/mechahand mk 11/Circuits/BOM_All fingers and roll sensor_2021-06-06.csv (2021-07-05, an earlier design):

ID | Name | Designator | Footprint | Quantity | Manufacturer Part | Manufacturer | Supplier | Supplier Part | Price | JLCPCB Part Class | LCSC Assembly
1 | ADS1115IDGSR | AADC1,BADC1,CADC1,DADC1,EADC1 | MSOP-10-DOT-BOT-LEFT | 5 | ADS1115IDGSR | TI | LCSC | C37593 | 2.952 |  | Yes
2 | 1uF | ACLP2,ACLP3,ACLP4,BCLP2,BCLP3,BCLP4,CCLP2,CCLP3,CCLP4,DCLP2,DCLP3,DCLP4,ECLP2,ECLP3,ECLP4 | C0603 | 15 | CL10A105KB8NNNC | SAMSUNG | LCSC | C15849 | 0.0083 | Basic Part
3 | 100nF | ACADC1,ACPOT1,ACPOT2,ACPOT3,ACREF1,BCADC1,BCPOT1,BCPOT2,BCPOT3,BCREF1,CCADC1,CCPOT1,CCPOT2,CCPOT3,CCREF1,DCADC1,DCPOT1,DCPOT2,DCPOT3,DCREF1,ECADC1,ECPOT1,ECPOT2,ECPOT3,ECREF1,RCPOT1 | C0603 | 26 | CC0603KRX7R9BB104 | YAGEO | LCSC | C14663 | 0.0041 | Basic Part
4 | FPC 0.5MM 6P MALE PCB PATTERN, BOTTOM COPPER | AP1,BP1,CP1,DP1,EP1 | FPC-PCBPATTERN-6P05PITCH | 5 | FPC 0.5MM 6P Pull type H2.0mm Pick up
5 | AS5600-ASOT | APOT1,APOT2,APOT3,BPOT1,BPOT2,BPOT3,CPOT1,CPOT2,CPOT3,DPOT1,DPOT2,DPOT3,EPOT1,EPOT2,EPOT3,RPOT1 | SOIC-8_L5.0-W4.0-P1.27-LS6.0-BL | 16 | AS5600-ASOT | Advanced Monolithic Systems | LCSC | C499458 | 1.4287 | Extended Part
6 | 2K | ARADC1,ARADC2,BRADC1,BRADC2,CRADC1,CRADC2,DRADC1,DRADC2,ERADC1,ERADC2 | R0603 | 10 | 0603WAF2001T5E | UniOhm | LCSC | C22975 | 0.0014 | Basic Part
7 | 10K | ARSDA1,ARSDA2,ARSDA3,BRSDA1,BRSDA2,BRSDA3,CRSDA1,CRSDA2,CRSDA3,DRSDA1,DRSDA2,DRSDA3,ERSDA1,ERSDA2,ERSDA3,RRPOT1 | R0603 | 16 | 0603WAF1002T5E | UniOhm | LCSC | C25804 | 0.0014 | Basic Part
8 | BF350-3AA | ASG1,ASG2,ASG3,ASG4,ASG5,ASG6,BSG1,BSG2,BSG3,BSG4,BSG5,BSG6,CSG1,CSG2,CSG3,CSG4,CSG5,CSG6,DSG1,DSG2,DSG3,DSG4,DSG5,DSG6,ESG1,ESG2,ESG3,ESG4,ESG5,ESG6 | BF350-3AA | 30
9 | _ | I2C |  | 1

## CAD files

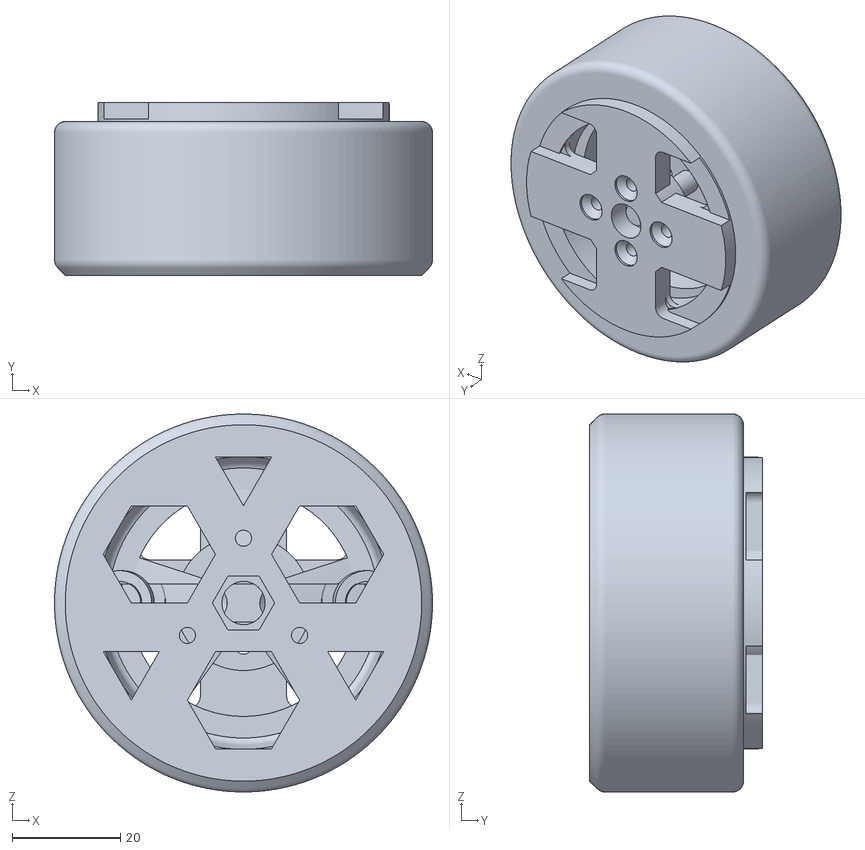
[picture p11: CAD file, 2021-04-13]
arm_model/Mecharm 3/Strain wave drive/Strain wave drive 42x assembled.stl
70.0 x 32.0 x 70.0

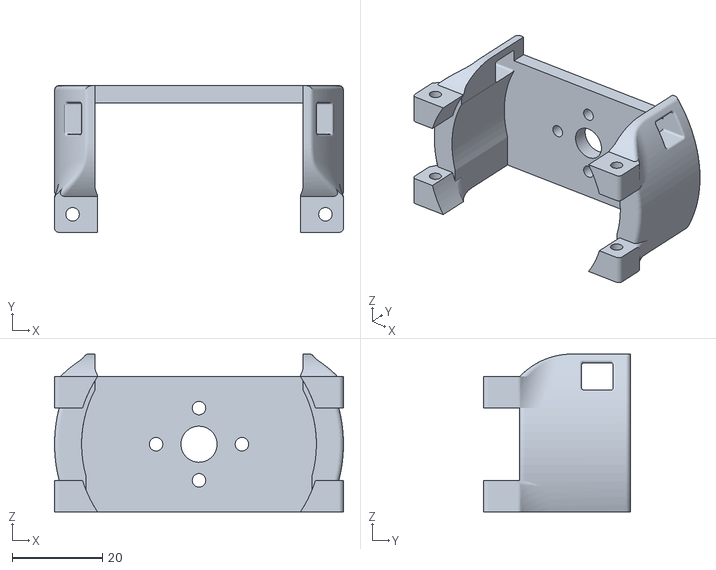
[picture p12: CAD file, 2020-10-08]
arm_model/Mecharm 2/cycloidal half/Motor mount.stl
64.0 x 32.5 x 35.0

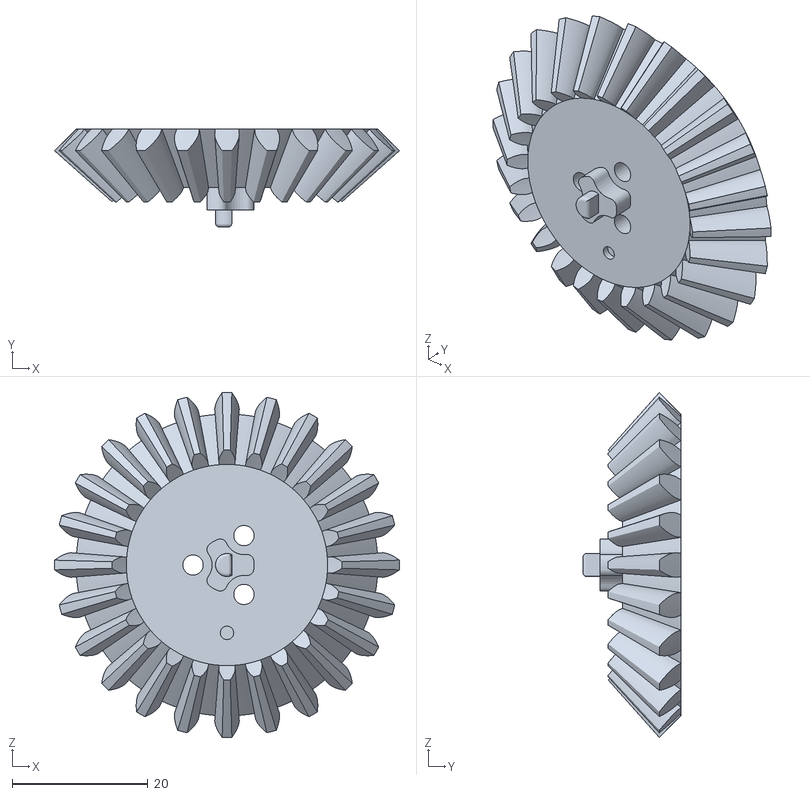
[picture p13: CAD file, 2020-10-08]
arm_model/Mecharm 2/Differential gear(Mirror).stl
50.8 x 14.4 x 50.8

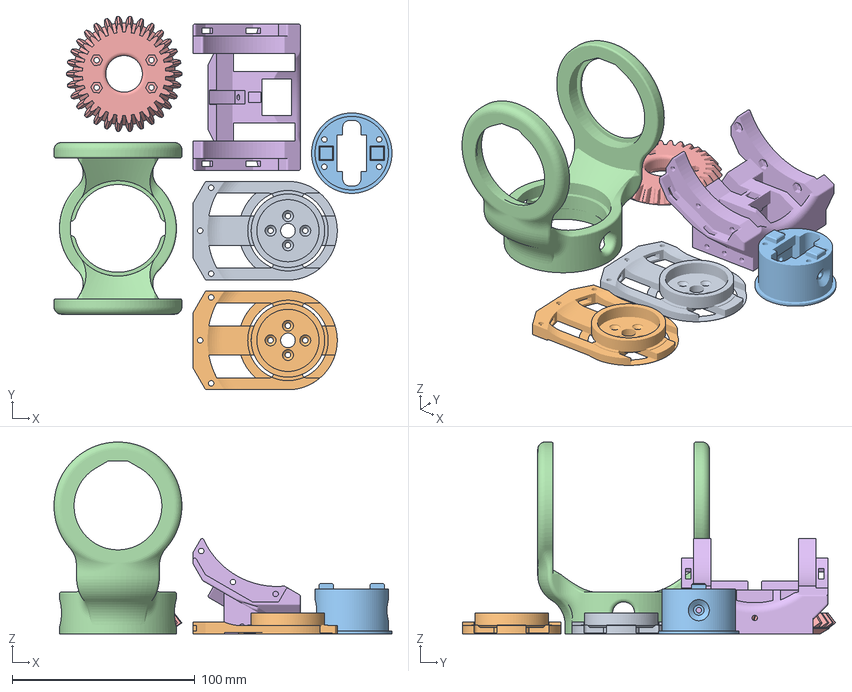
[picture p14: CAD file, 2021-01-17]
arm_model/Mecharm 3/Strain differential/Strain differential structure.3mf
184.9 x 204.3 x 105.0 mm
Bridge cap.stl
Base mount.stl
Gimbal structure.stl
Pinion.stl
Actuated mount.stl

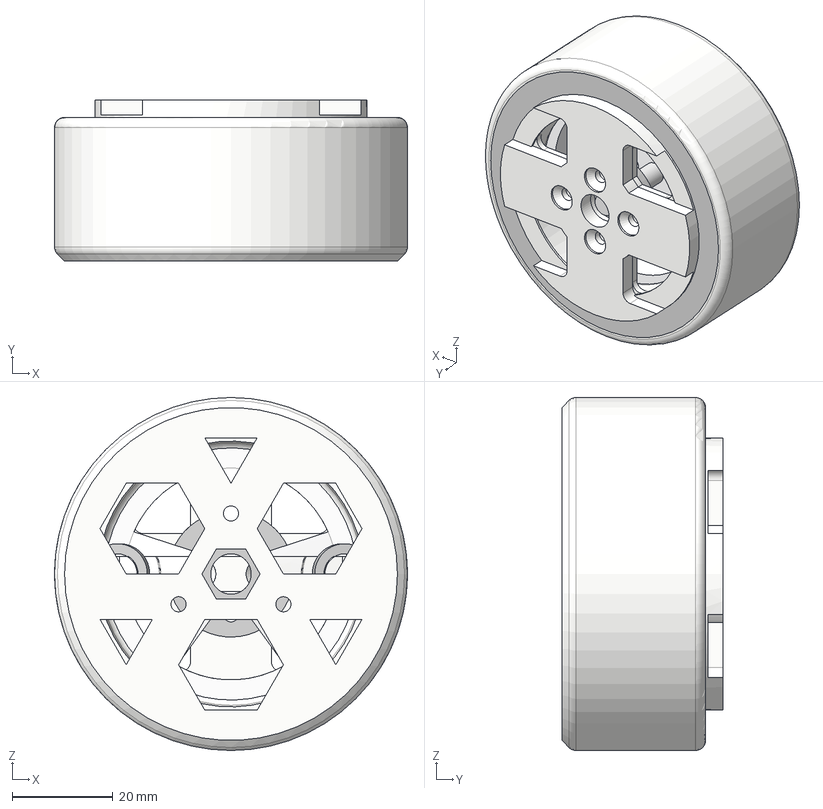
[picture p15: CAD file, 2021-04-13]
arm_model/Mecharm 3/Strain wave drive/Strain wave drive 30x.step
70.0 x 32.0 x 70.0 mm
Brushless motor 5010 360KV 12N14P
6810-2RS Ball bearing
MR128ZZ Ball Bearing x 3
Flex spline
Actuated spline
Wave generator
Mount and cap

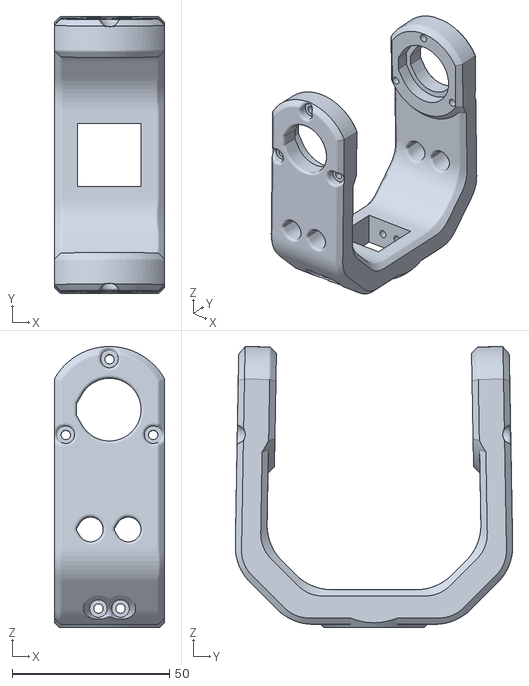
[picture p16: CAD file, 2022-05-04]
arm_model/Mecharm 4 belt differential/Output brace.stl
35.2 x 88.4 x 89.5

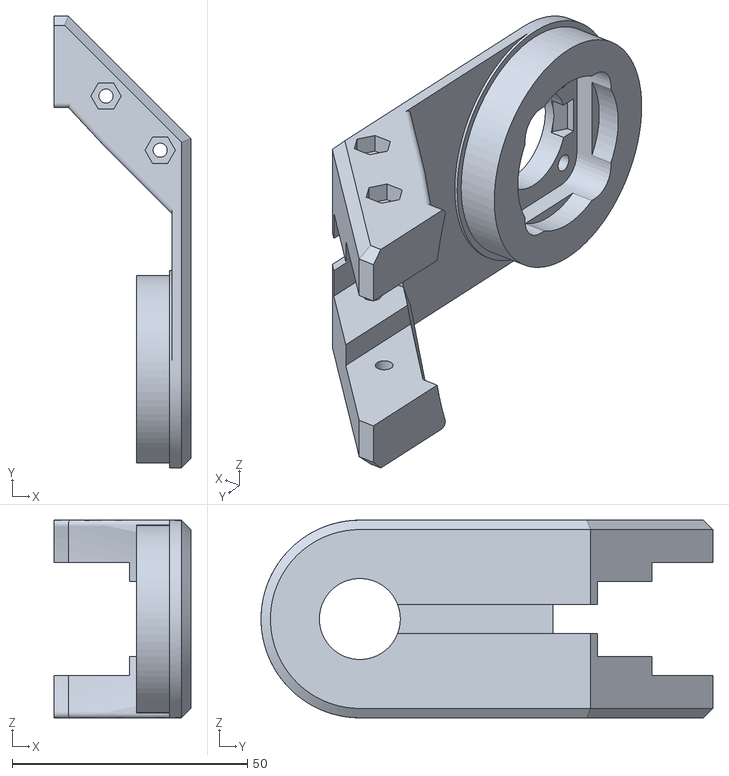
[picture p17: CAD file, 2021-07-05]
arm_model/Mecharm 4 strain differential/Side bracket right.stl
29.0 x 96.0 x 42.0

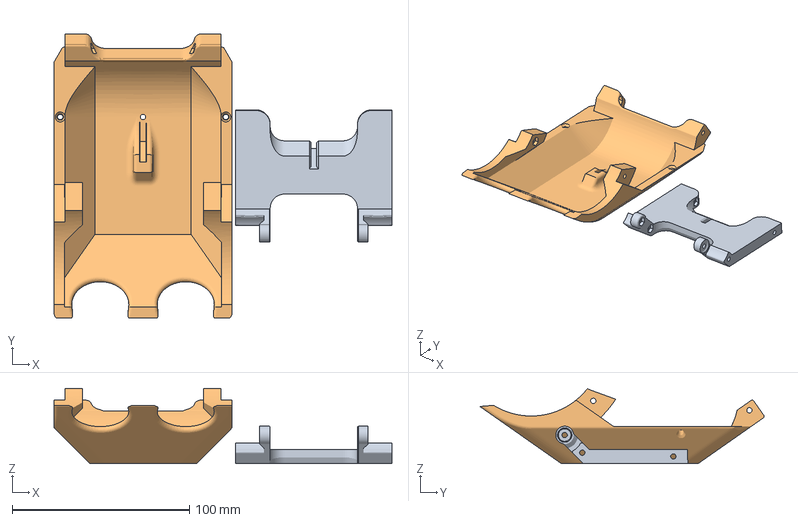
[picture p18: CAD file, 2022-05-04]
arm_model/Mecharm 5 dual stage belt differential/Frame covers.3mf
190.6 x 160.3 x 42.3 mm
Frame bottom cover.stl
Frame cover.stl

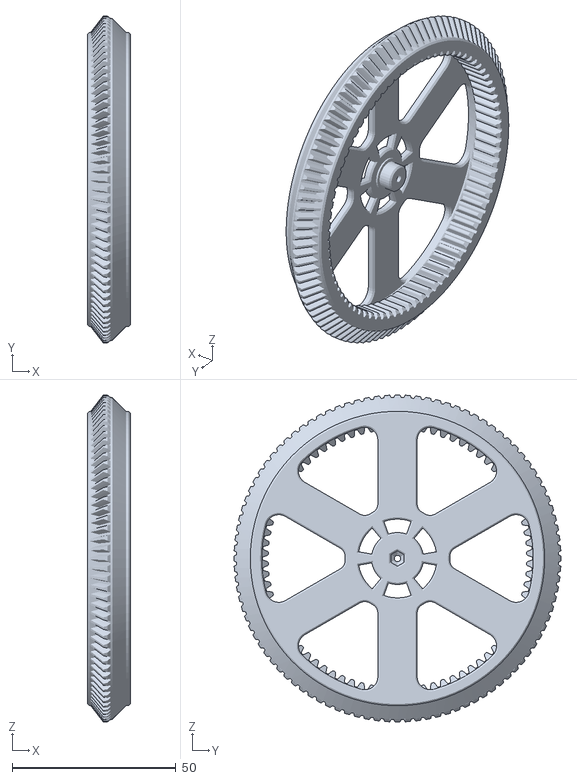
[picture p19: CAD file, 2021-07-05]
arm_model/Strain wave 4/Side gear.stl
13.0 x 100.0 x 100.0

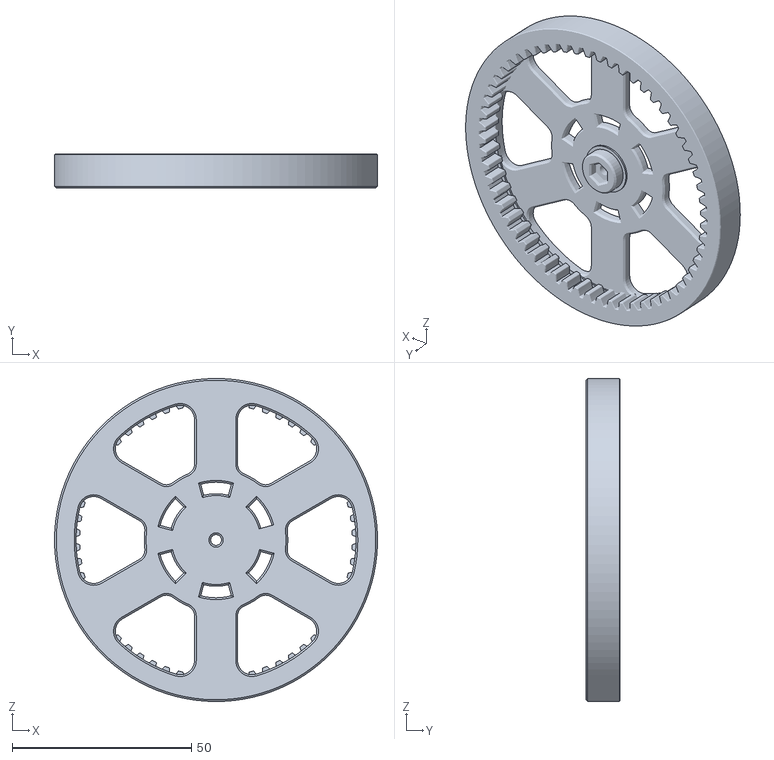
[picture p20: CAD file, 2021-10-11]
arm_model/Strain wave 5 (30x)/Output gear.stl
90.0 x 9.50 x 90.0

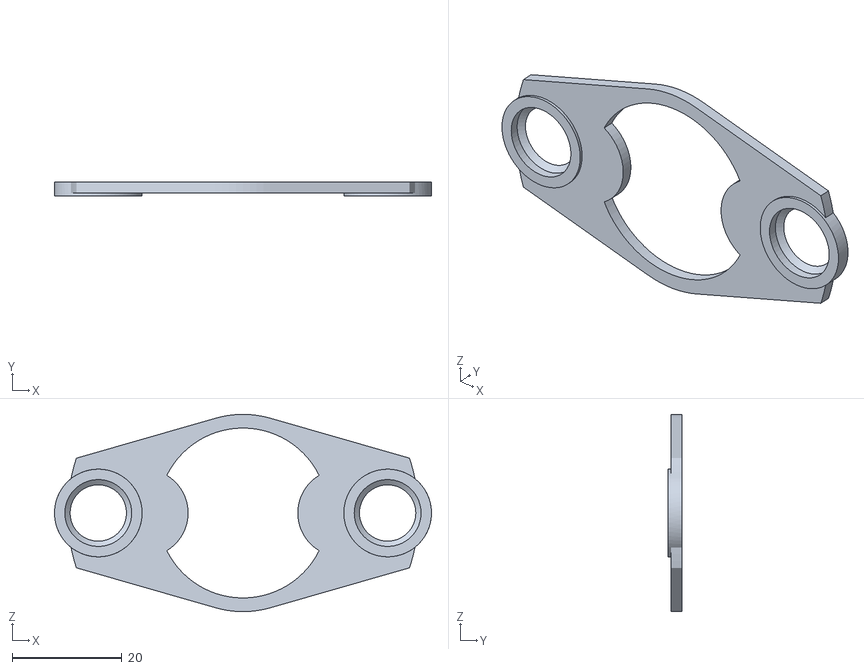
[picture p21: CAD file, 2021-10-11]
arm_model/Strain wave 5 (60x)/Wave generator cap.stl
68.8 x 2.50 x 36.0

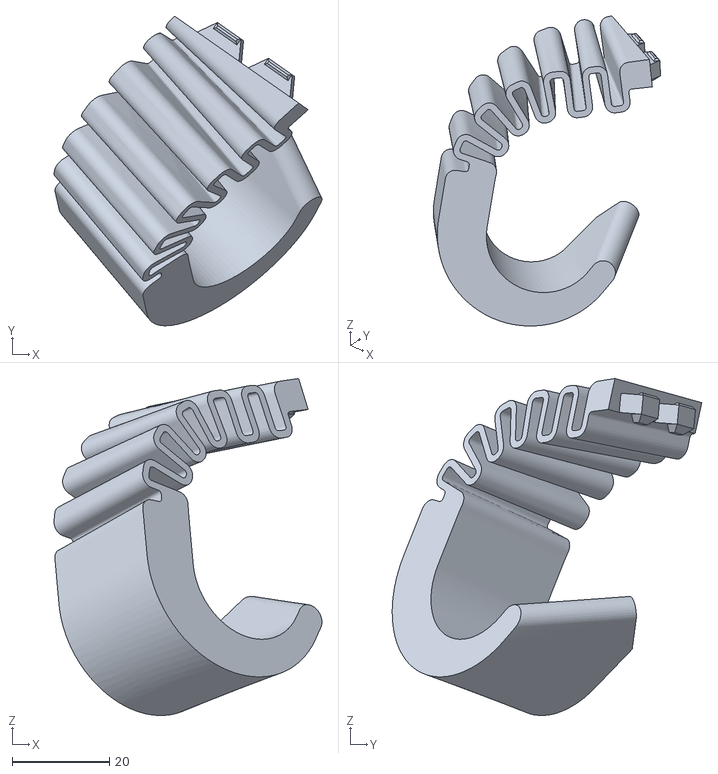
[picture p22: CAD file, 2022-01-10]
glove_model/Clampy glovey/Thumb wrap.stl
55.2 x 63.8 x 69.4

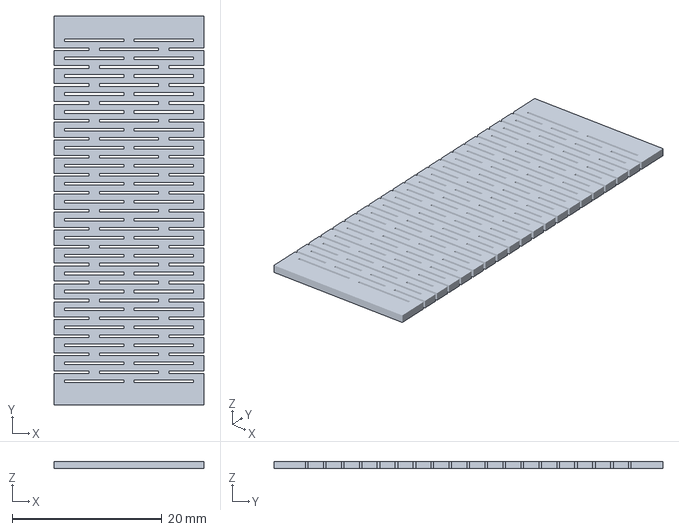
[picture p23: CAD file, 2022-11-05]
glove_model/Experiments/Mesh strip.3mf
20.0 x 52.0 x 1.00 mm

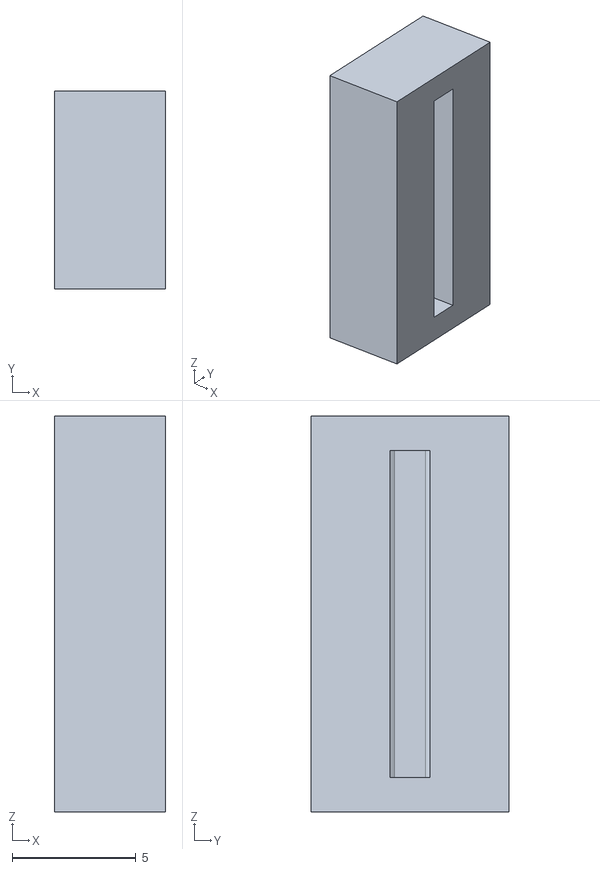
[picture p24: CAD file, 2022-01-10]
glove_model/Snakey pin module/Fixed receptacle.stl
4.50 x 8.00 x 16.0

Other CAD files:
glove_model/Test glove/Floating strap.stl
glove_model/Test once piece glove/Glovey.stl
glove_model/Windup spindle module/Spring making rod.stl
hand_model/experiments/bidirectional joint module/Support.stl
arm_model/Mecharm 2/Differential gear.stl
arm_model/Mecharm 2/Differential gears.3mf
arm_model/Mecharm 2/Differential pot mount(Mirror).stl
arm_model/Mecharm 2/Differential pot mount.stl
arm_model/Mecharm 2/Differential pot mounts.3mf
arm_model/Mecharm 2/Drive cover.stl
arm_model/Mecharm 2/Elbow hand mount.stl
arm_model/Mecharm 2/Elbow rod mount.stl
arm_model/Mecharm 2/Mount.3mf
arm_model/Mecharm 2/Mount.stl
arm_model/Mecharm 2/Shoulder bearings support.stl
arm_model/Mecharm 2/Shoulder rod mount.stl
arm_model/Mecharm 2/Shoulder swing gear.stl
arm_model/Mecharm 2/Shoulder swing mount.stl
arm_model/Mecharm 2/cycloidal half/Actuated cap.stl
arm_model/Mecharm 2/cycloidal half/Actuated.stl
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

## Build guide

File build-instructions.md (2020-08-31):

Building Hextech Mechahand mk 10
================================

Components and tools
--------------------

Buy all the parts required in the [bill of materials](bill-of-materials.md).

Order mostly assembled driving PCBs using the gerber files from `24drive`. Designed for assembly by jlcpcb.com, the
pick and place and electronics bill of materials are also available in the required formats. Manual assembly of the
driving PCB would require separately purchasing and soldering surface mount components. Machine assembly is better!

You should also prepare the following tools, and know how to use them:
* Protective glasses! PLA and nylon wires break suddenly and throw shards.
* 3D printer. Components are designed to be printed with 0.4mm nozzle FDM printer. Resin printers should also work.
* Soldering iron, solder, flux, and bronze sponge. Position encoders are embedded in plastic and soldered in place, practice fast soldering.
* Voltmeter. Need to test all connections after soldering, especially the strain gauges.
* LiPo charger and preferably a LiPo fireproof safe.
* Pliers, cutters, and tweezers. Multiple types of pliers recommended; flat for placing parts, round for handling wires, sharp for cutting tough nylon braid.
* Screwdriver or hex key with M3 head. Preferably a motorized screwdriver, there's going to be a lot of screwing.
* Crimping tool.
* Hammer!

Electronics
-----------

Order assembled PCBs from jlcpcb.com or your choice of supplier using design files in the `24driver/PCB`
directory. Place and solder the ESP32, the OLED screen andthe button on the populated side of the PCB.
Trim the legs of the Buck converter and solder it to the bottom side. Skip the capacitor bank! Place and
solder 6 JST PH 3-pin connectors for the pressure sensors, leave the 6 center-right connectors free and
cover with electric tape; the wrist roll motor will rest directly underneath this space. Place and solder
24 JST PH 2-pin and 3-pin connectors for the 6 rows of position and motor channels.

Mechanics
---------

Print all 3D parts from the latest `hand_model`. Can use the gcode directly for a Mk3 Prusa printer, or
the `3mf` design files. Need 5 fingers and finger skins, 5 motor systems, 2 mini worm joints, 2 worm joints,
and 1 of everything else.

### 1. Case

1. Place the plastic button cover on the electronic button and place the board into the PCB case with the hexagonal decal.
2. Slide the case and case shelf piece together and fix with 4 8mm hex screws and embedded nuts.

TODO: finish instructions...

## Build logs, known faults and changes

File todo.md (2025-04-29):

Circuit
-------

Use MT6701QT-STD because it's teeny tiny and < 1mm height.

[ ] Very important, move logo 3 mm to the side on the fingertip so it can be seen from outside.
[ ] Totally not important, default the motor drivers to sleep state when controller off also cause it's
a strapping pin for the ESP32...
[x] Slight increase to spacing of fingertip pressure sensors. Fix top folding, just offset pads a bit and
bend during assembly.
[x] Modify motor layout for 17mm motor spacing; use the extra space and go back to the new motor drivers.
[ ] Add at least a button; dedicate it to reset the wifi or something.

Done
====

[v] Finish first fully working prototype (with remote hand mimicking).
[x] Write pending blogposts on modeling, circuit, and mk 4&5 hands.
[v] Update PCB with compact design, all 3V3 logic, 5V DC-DC converter (replacing volt reg also leads to 24V rating).
[v] Write bill of materials.
[x] Document assembly.
[x] Publish first working version.
[v] Connect the pid drive shift register to the reset line. After a reset the arduino pulls the pins high, which causes the motors to move if the shift register outputs are also high.
[x] To potentially make the reset programmable, leave SR reset alone, but add pull-down resistors to the all motor driver inputs.
    Inbuilt pull down resistors, now all inputs are connected to shift registers which are explicitly 0ed at power up.
[v] Fix the PID drive arduino programming deal. The arduino powers the motor drivers when connected to 5V internally, this causes the motors to work. Need to pull the PWM or RX/TX output
signals low to prevent motors working during programming.
    Done, arduino no longer turns motors at startup, and RX/TX lines are free.
[v] Fix the main board encoders. They need a stronger pull up resistor (10K ohm), otherwise the esp32 keeps interrupting itself. Also a low pass filter or something.
    Pull-ups and low passes for all inputs.
[v] Change voltage to 7V4, cause I misremembered.
    Changed on driver board. Changed on main board.
[v] ! Fix the address pins on the nano. Dual use doesn't work if there's a LED on the same pin. Also avoid pin 13 as it has the internal LED. Increasing the LED resistance to 10K ohm works, but it's a bit dodgy.
    Fixed, LED moves to it's own pin.
[v] Not a good idea to connect the main chip 5V to the driver chip 5V, not the same 5V level because of different regulators. Also since a reset of
the main chip shuts down current for the driver chips, we might not need a reset line? TLDR: Redesign connectors to be more streamline.
    Connectors for the PID6 drive are now SCL SDA RST VCC GND, which is all lines needed as inputs.
[v] Change to 3V3 voltage for the inputs to the esp board. ESP can't read higher than it's working voltage.
[v] Enlarge the support holes for the encoders.
[v] Test soldering address pads.
    Tested, it's pretty difficult. Enhanced the solder mask to allow a bridge between the pads.
[v] Double check current sensor pins are properly upside down.

Improvements
------------

[v] Sturdier finger covers, maybe screwed on. Make them easier to put on (no inside prongs). Try to cover joints too?
[v] Integrate finger covers as structural outer shell.
[v] Joint potentiometer housing should also have mounting channels for the wires. Was a good idea!
[x] Flatten hand design:
  * Pitch axis further back and in-line with yaw.
  * Fingers yaw pivot on top of abduct. No need for big hole in finger cover.
  * Bring fingers lower, and cover bottom of pinky/thumb pivots.
[v] Compact hand design, with inline tendon wires and inline thumb and pinky pivots.
[v] Housing improvements:
  * Smaller housing for compacter PCB.
  * Hand interface as separate piece that screws on the bottom of the main chassis. Easier to screw from below.
  * Mounting pins from interface to PCB housing.
[v] Switch to 12V using 4s LIPO battery, 12V motors and improved PCB (DC-DC buck converter).
[v] Better pressure sensor design:
  * Put gauges on opposite sides, directed so one stretches and one compresses, doubling signal.
  * Is sensitive enough to put on main structure?
  * Make sensor easier to build/solder. Maybe individual wire channels? Flatter gluing area.

Driver Redesign
---------------

[v] Try to redesign the driver as a single PCB with 24 driving channels + sensors option.
[v] Smoothing capacitor is connected in parallel. Absolutely no use with the short circuit behaviour of the TB6612FNG...
  Still including it in, but smaller 4.7uF cap to smooth out 100kHz frequency. Can use both quick brake and slow brake mode with new driver chips.
[v] De-solder smoothing capacitors, was stupid idea cause it crosses the short-circuit current limit within a 100kHz cycle.

ESP
---

[v] Select input to which joint.
[v] Select output to which joint.
[v] Select min and max of each joint target.
[v] Same as above, but for the I2C nano joints.
[v] Save joint config on NVS on the ESP32.
[v] Measure power. And calibrate.
[v] Connect to wifi. If I can, go straight via the BLE api.
[v] Websocket with joint position, target, min, max via json.
[v] Measure tip pressure via precise ADC IC.

### PCB

[v] Draw board layout.
[v] Place parts on printed PCB and order.
[x] Maybe put a coil in series with the power so we limit the current on turning on.
Since motor capacitance will charge up on power-up.
[v] P-channel mosfet power switch. Hmm.
[x] Re-design and order the sensors mini board. No need, sensors board is enough.

Nano
----

[v] Select which input to which joint.
[v] Select which output to which joint.
[v] PID drive joint to target.
[v] Set P, I, D, threshold, overshoot, direction settings for each joint.
[v] Drive joint for duration at power.
[v] Set different 0 output point to allow some way of adding pressure with the motors.
[v] Get joint position.
[v] 2 input pins for address selection so only need 1 program to upload.
[v] Error handling for the I2C.

### PCB

[v] Draw board layout.
[v] Build board for the copper prototype pads.
[v] Place parts on printed PCB and order.
[v] Assemble boards.
[v] Test boards.

Demo Page
---------

[v] Page with joint position graph and control slider underneath.
[v] Connect via websocket to hand.

Hand
----

[x] Make spindle shorter and better middle rail so nylon doesn't slip even on when over-driven. Maybe reduce the tensioner angle?
[v] Make holes for spindle wires so it channels the wire better.
[x] Edit motor holder to have top support for motor ... (made holder less bendy instead)
[v] ... and higher/tighter spindle blocker.
[v] Re-make hand using new fingers.
[v] Better leverage for thumb and pinkie carriages.

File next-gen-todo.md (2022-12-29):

Next generation hand ideas
==========================

[v] Custom order coreless motors with planetary gearbox that can withstand 10kg force on the tendons!
[ ] Add rotation encoder to motors and connect via flex circuit to an FPC connector on the driver board. Maybe add temperature sensor directly on top of motor too. No more soldering!
[ ] Use STM32 chips to control pairs of 2 motors and read all the inputs from them. We'll need them to be able to run the fast current control loop without interruptions from main micro controller.
[ ] Directly assemble the ESP32 chip, use the one with the integrated USB C driver.
[ ] Program in remote updates for the ESP32 chips, and also program the ESP32 master controller to be able to program the STM32 motor controllers.
[ ] Test paper display and switch to it, use FPC connector on board again.
[?] Fan output from main board. Maybe temperature sensor somewhere in middle, but not needed if we put the temp sensors on the motors.
^ Might not need the above because the new motors are strong enough within their continuous operating amperage of 0.5A.
[?] ROS compatibility. Only if anyone asks for it.

Previous gen done
=================

[v] Differential bevel gears on a U joint for the wrist. Big space for wires in the middle, very sturdy.
[v] Switch to coreless DC motors for quieter operation and greatly simplified circuitry. There's no way to output max torque from brushless motors at standstill without a position encoder on the motor shaft. Speed at which it starts working is about 1Hz electrical rotation. Coreless motors are lighter and quieter and should work just fine.
Coreless is near mandatory for backdrivabialiy.
[v] Alternatively 4 extra motors physically connected to each other as the 2 sides of the spindle. Tendon wires go out the middle and to the wrist and hand roll joints. Tensioning done by driving the gears.
Yep, works good.
motors in opposite sides then sliding and fixing the motors together.
[v] 4 spare inputs put on the tip joints (distal-medial) of non-thumb fingers. Tips are connected to driven joint (medial-proximal) by a spring. Difference in joint angles should be an accurate measure of tip force. More accurate then motor current feedback, will work passively too.
OMG it works!
[v] Switch to hall effect position sensors.
[v] Single ribbon cable between palm and wrist sensors to driver hand.
Works perfectly, needs proper channel to pass through nicely so it doesn't get pinched.
[v] CAN bus interface? Potential to drive robot arm, or be driven by robot arm. In any case robot arm needs separate control boards or daisy chained CAN bus.
Definitely needed.

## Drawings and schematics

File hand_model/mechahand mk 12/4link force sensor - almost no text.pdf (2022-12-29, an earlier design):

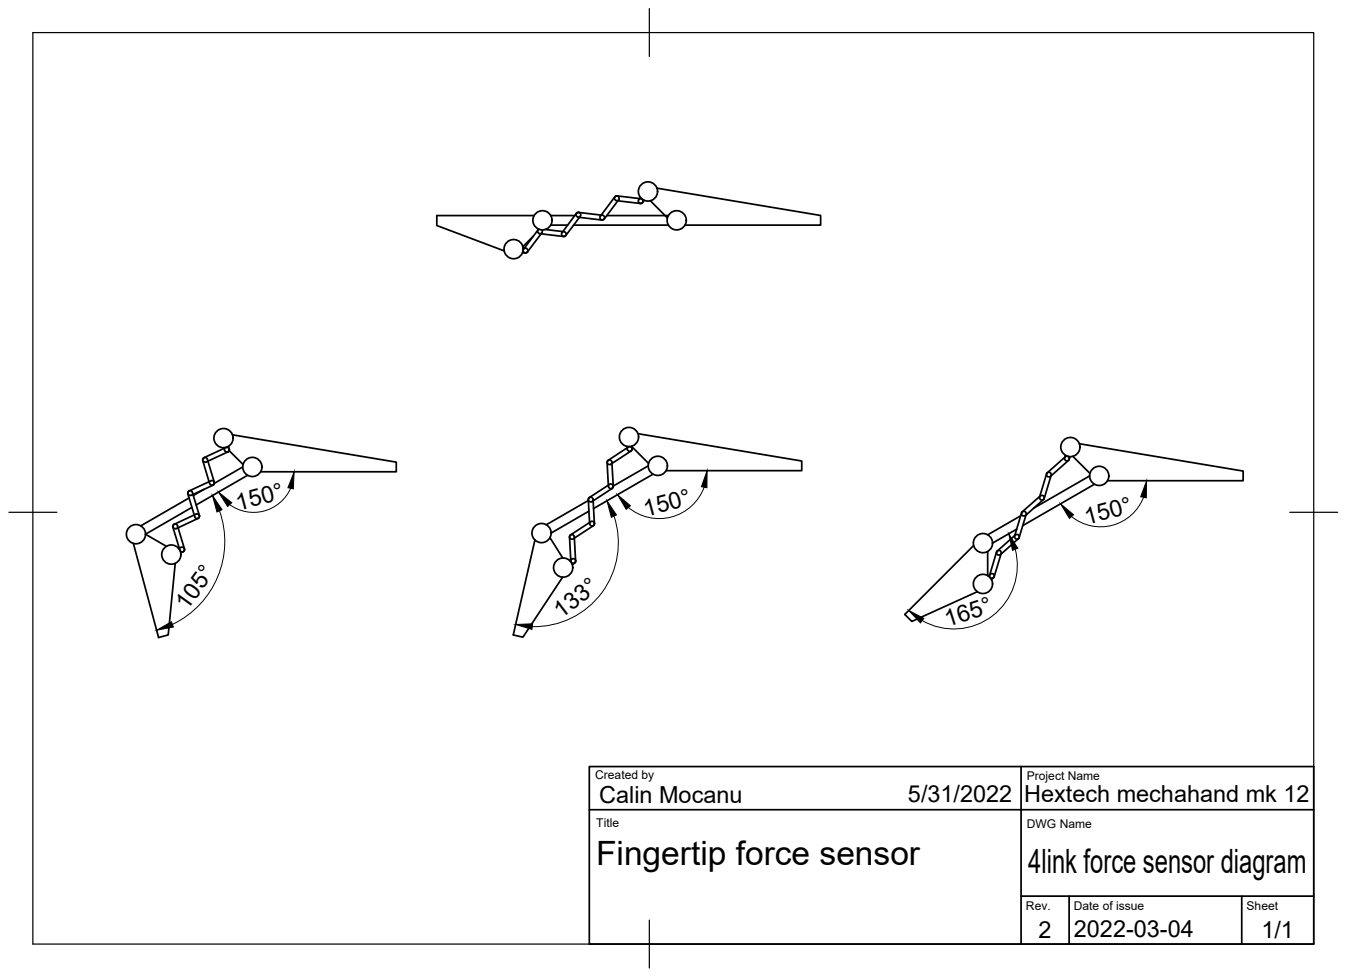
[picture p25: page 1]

Created by 5/31/2022 Calin Mocanu | Project Name Hextech mechahand mk 12

Title Fingertip force sensor | DWG Name 4link force sensor diagram

Rev. 2 | Date of issue 2022-03-04 | Sheet 1/1

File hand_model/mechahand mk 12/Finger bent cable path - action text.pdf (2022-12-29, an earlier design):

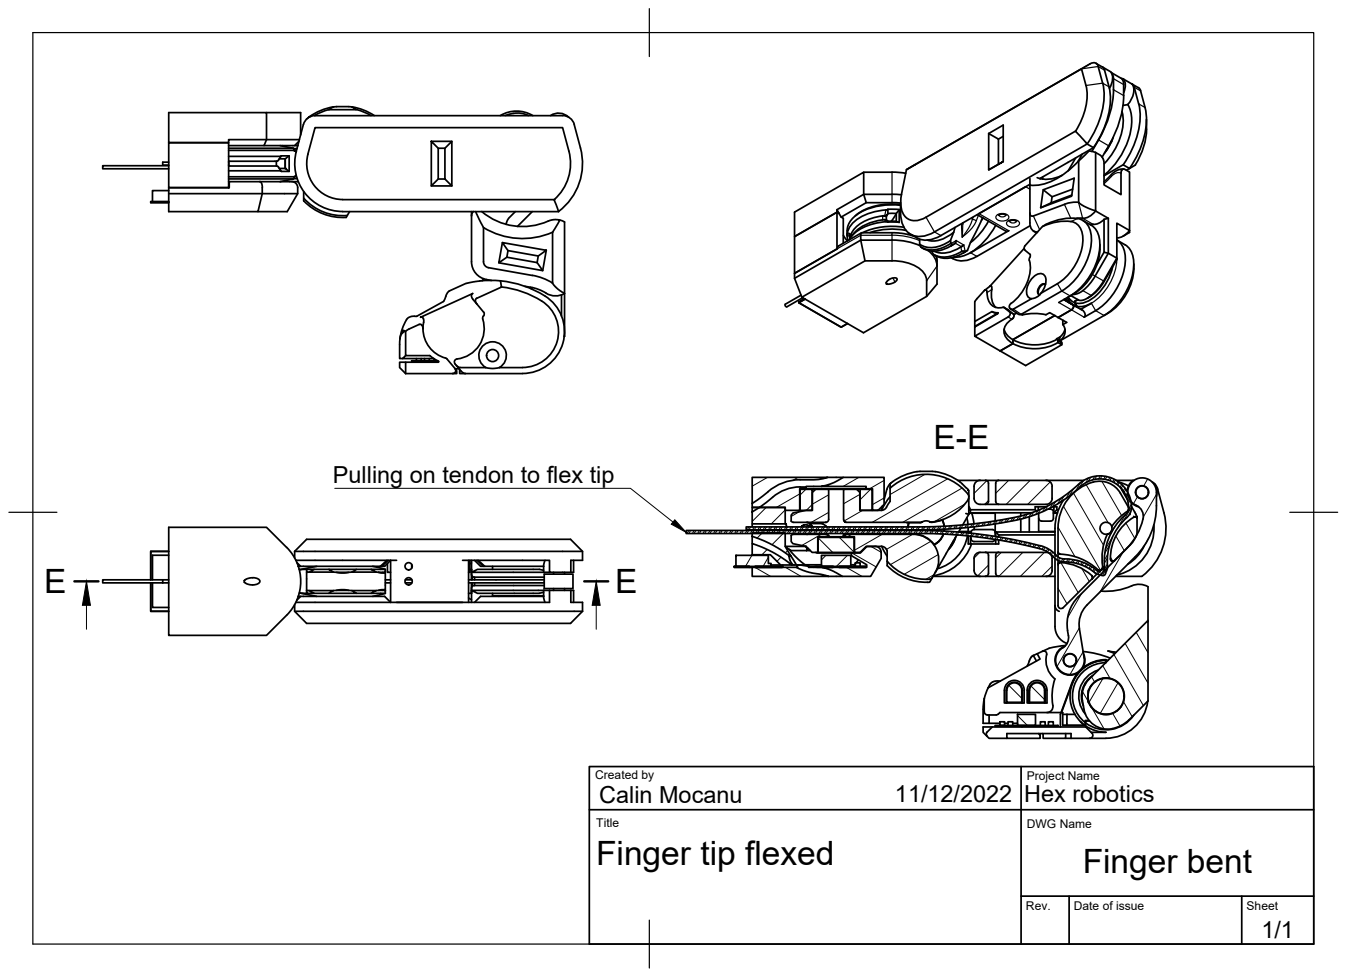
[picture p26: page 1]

Pulling on tendon to flex tip

Created by 11/12/2022 Calin Mocanu | Project Name Hex robotics

Title Finger tip flexed | DWG Name Finger bent

Rev. | Date of issue | Sheet 1/1

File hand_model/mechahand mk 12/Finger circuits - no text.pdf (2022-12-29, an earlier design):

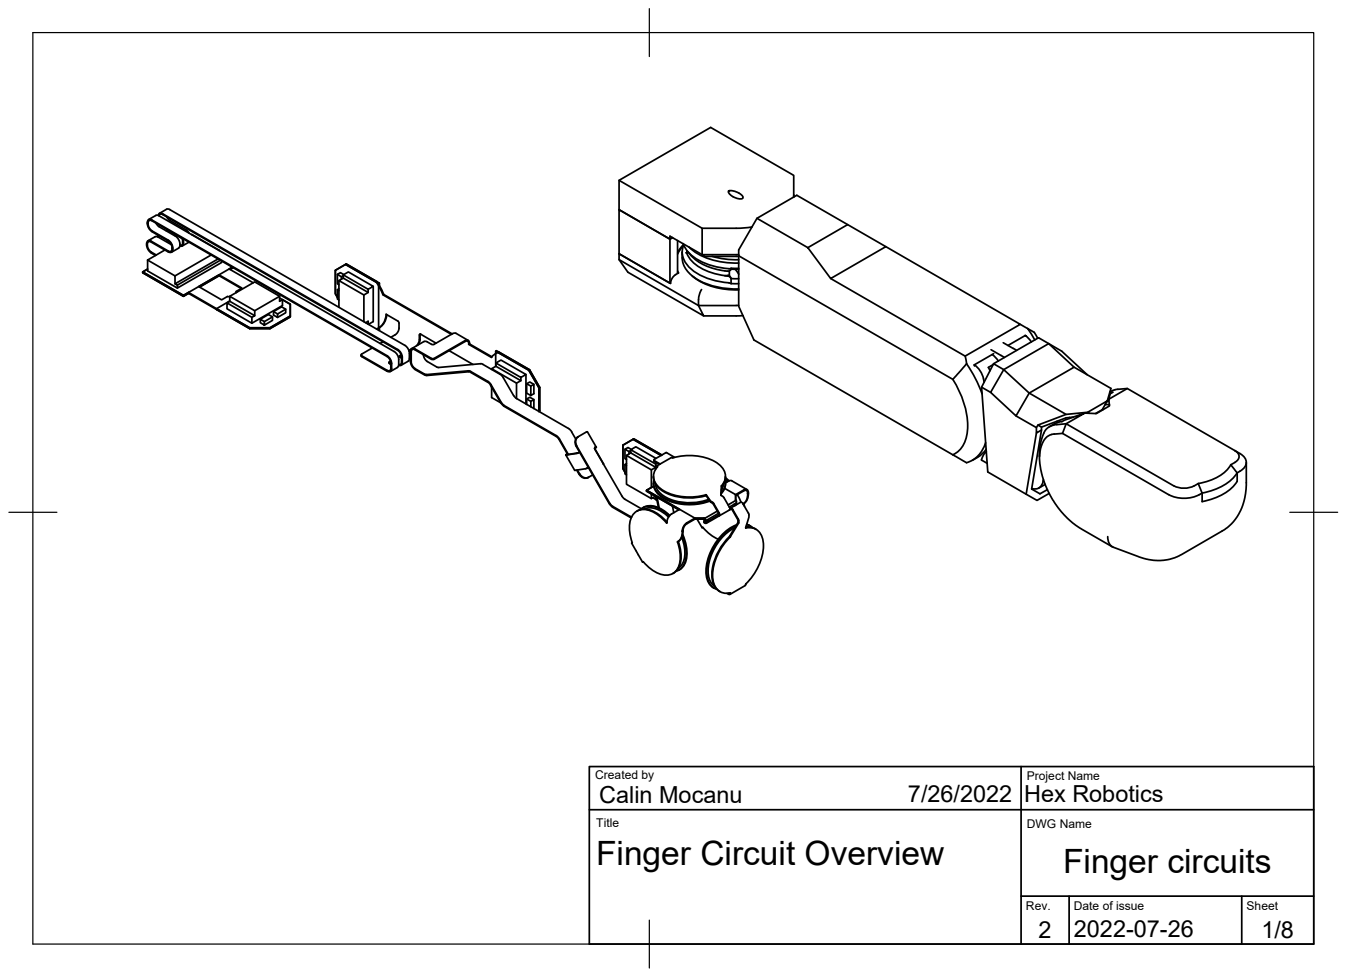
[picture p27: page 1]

Created by 7/26/2022 Calin Mocanu | Project Name Hex Robotics

Title Finger Circuit Overview | DWG Name Finger circuits

Rev. 2 | Date of issue 2022-07-26 | Sheet

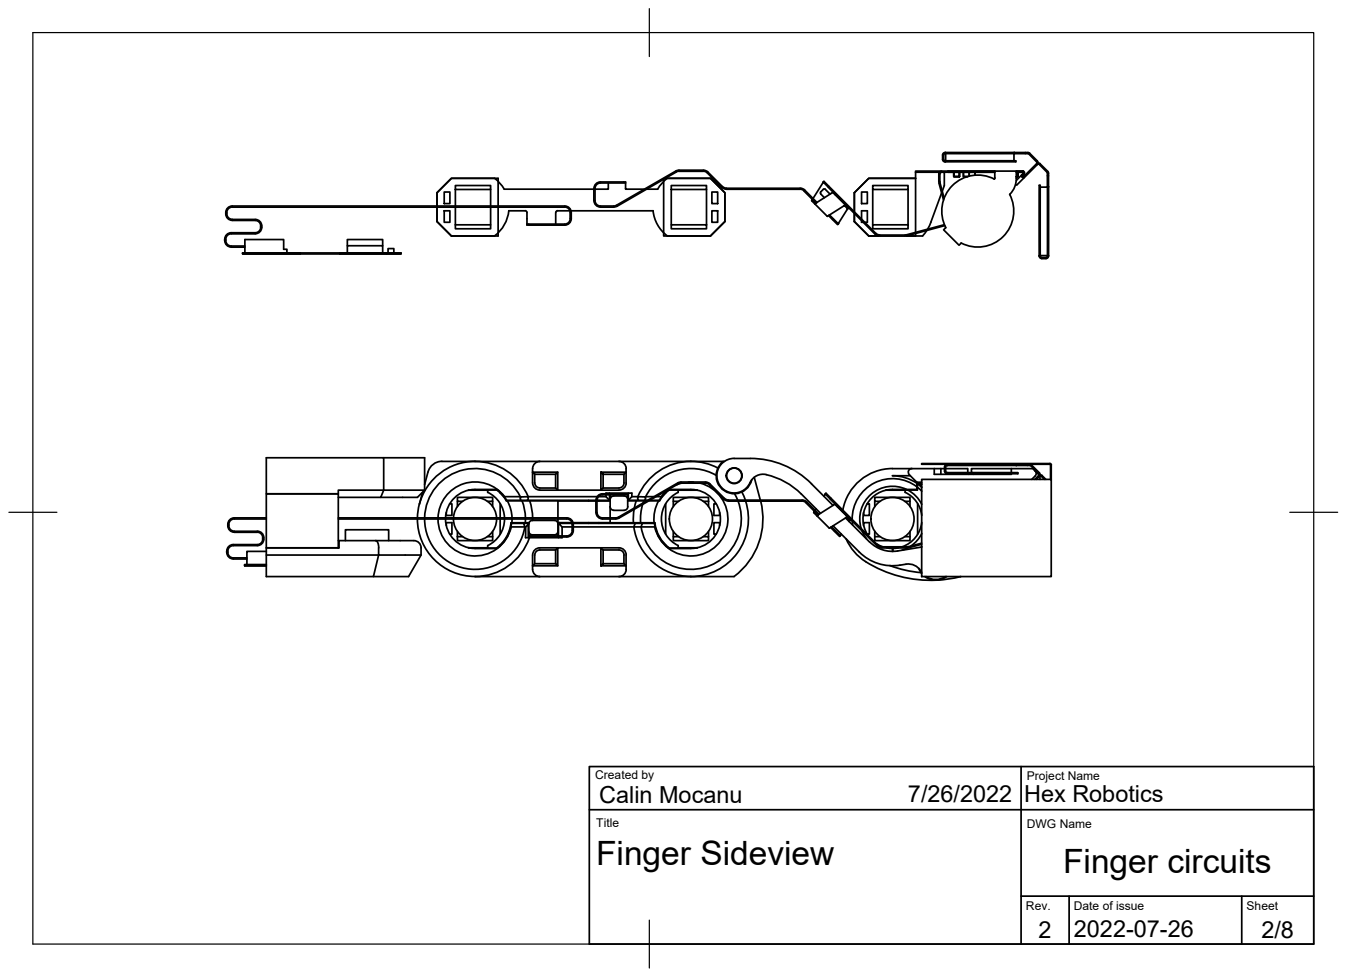
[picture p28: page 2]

Created by 7/26/2022 Calin Mocanu | Project Name Hex Robotics

Title Finger Sideview | DWG Name Finger circuits

Rev. | Date of issue | Sheet

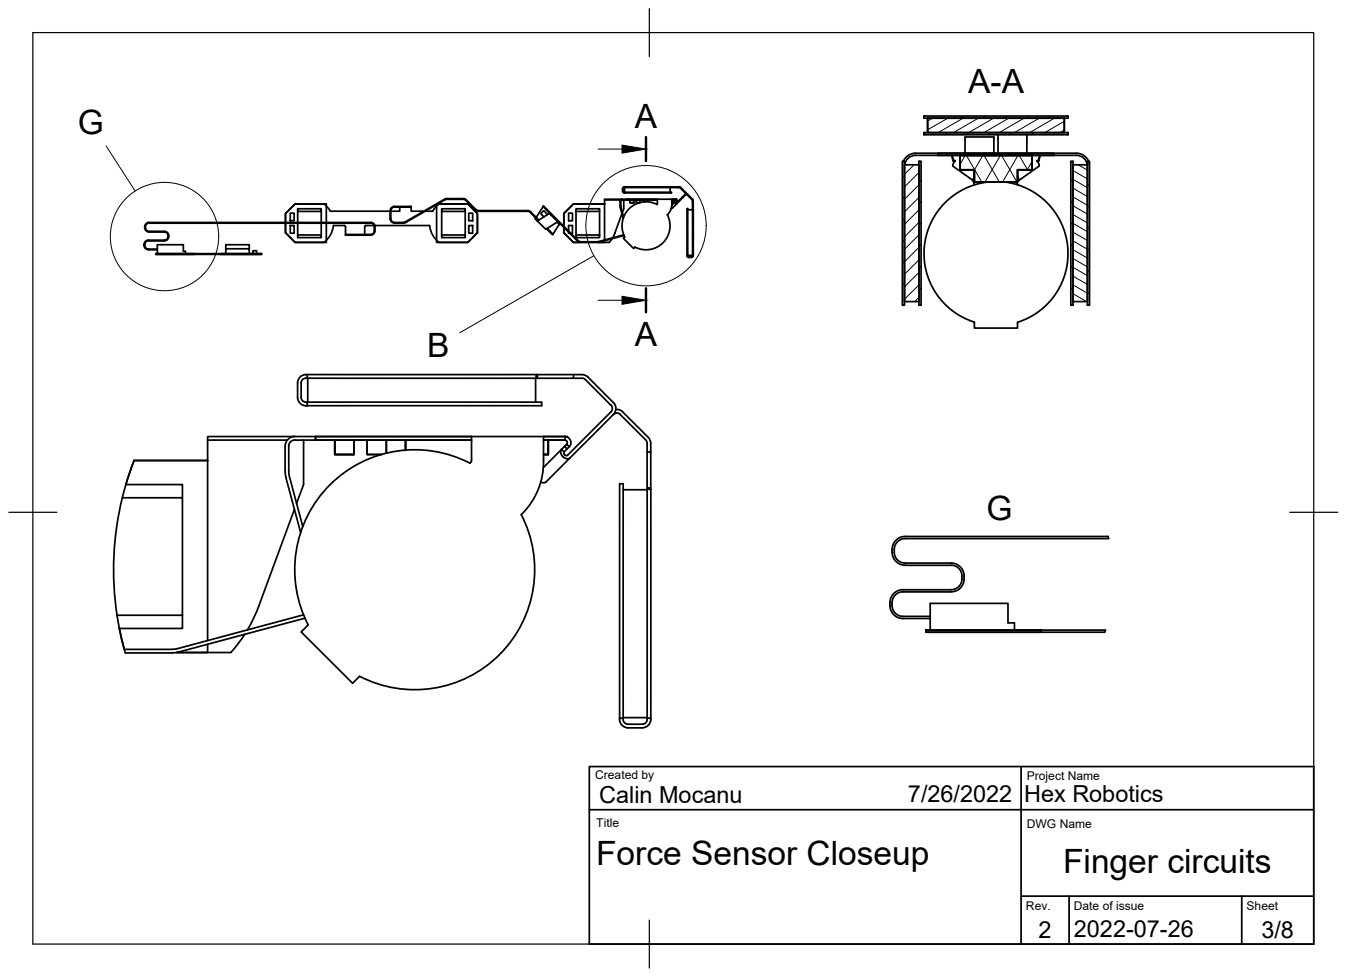
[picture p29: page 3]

Created by 7/26/2022 Calin Mocanu | Project Name Hex Robotics

Title Force Sensor Closeup | DWG Name Finger circuits

Rev. | Date of issue | Sheet

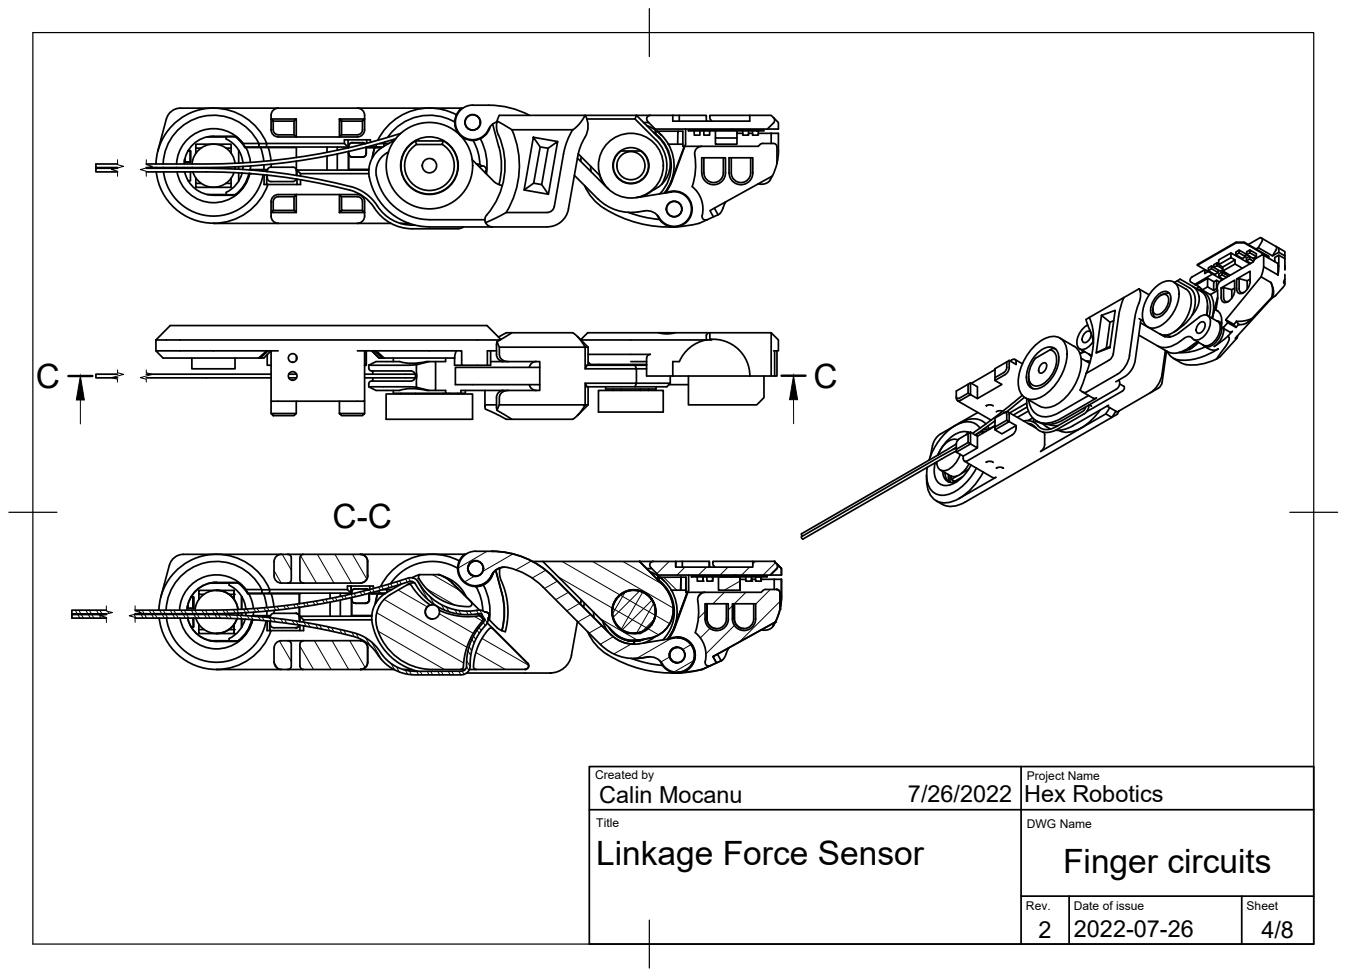
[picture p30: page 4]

Created by 7/26/2022 Calin Mocanu | Project Name Hex Robotics

Title Linkage Force Sensor | DWG Name Finger circuits

Rev. | Date of issue | Sheet

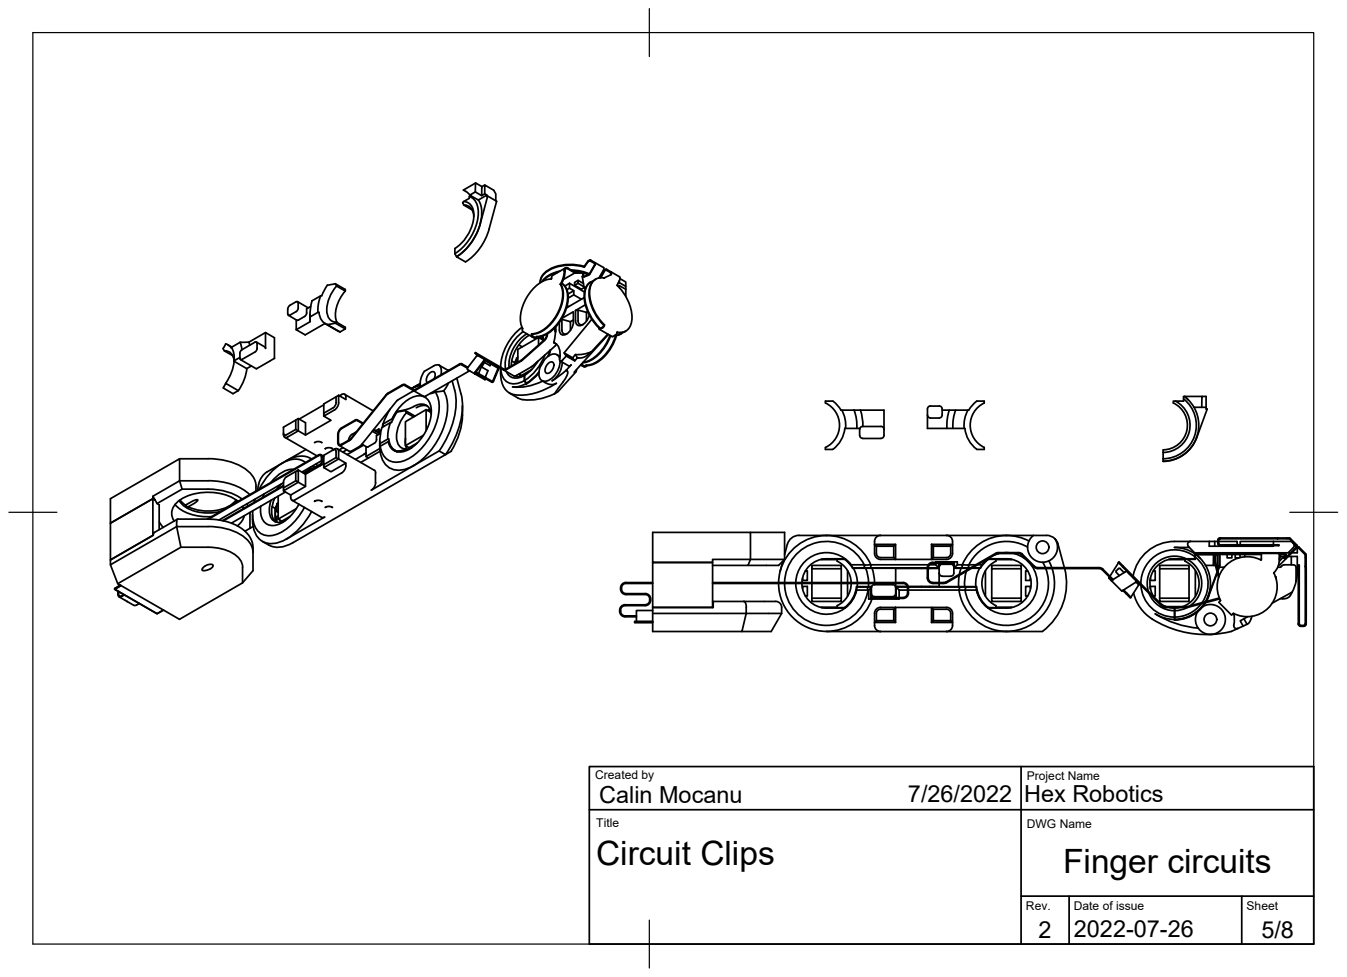
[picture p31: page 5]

Created by 7/26/2022 Calin Mocanu | Project Name Hex Robotics

Title Circuit Clips | DWG Name Finger circuits

Rev. | Date of issue | Sheet

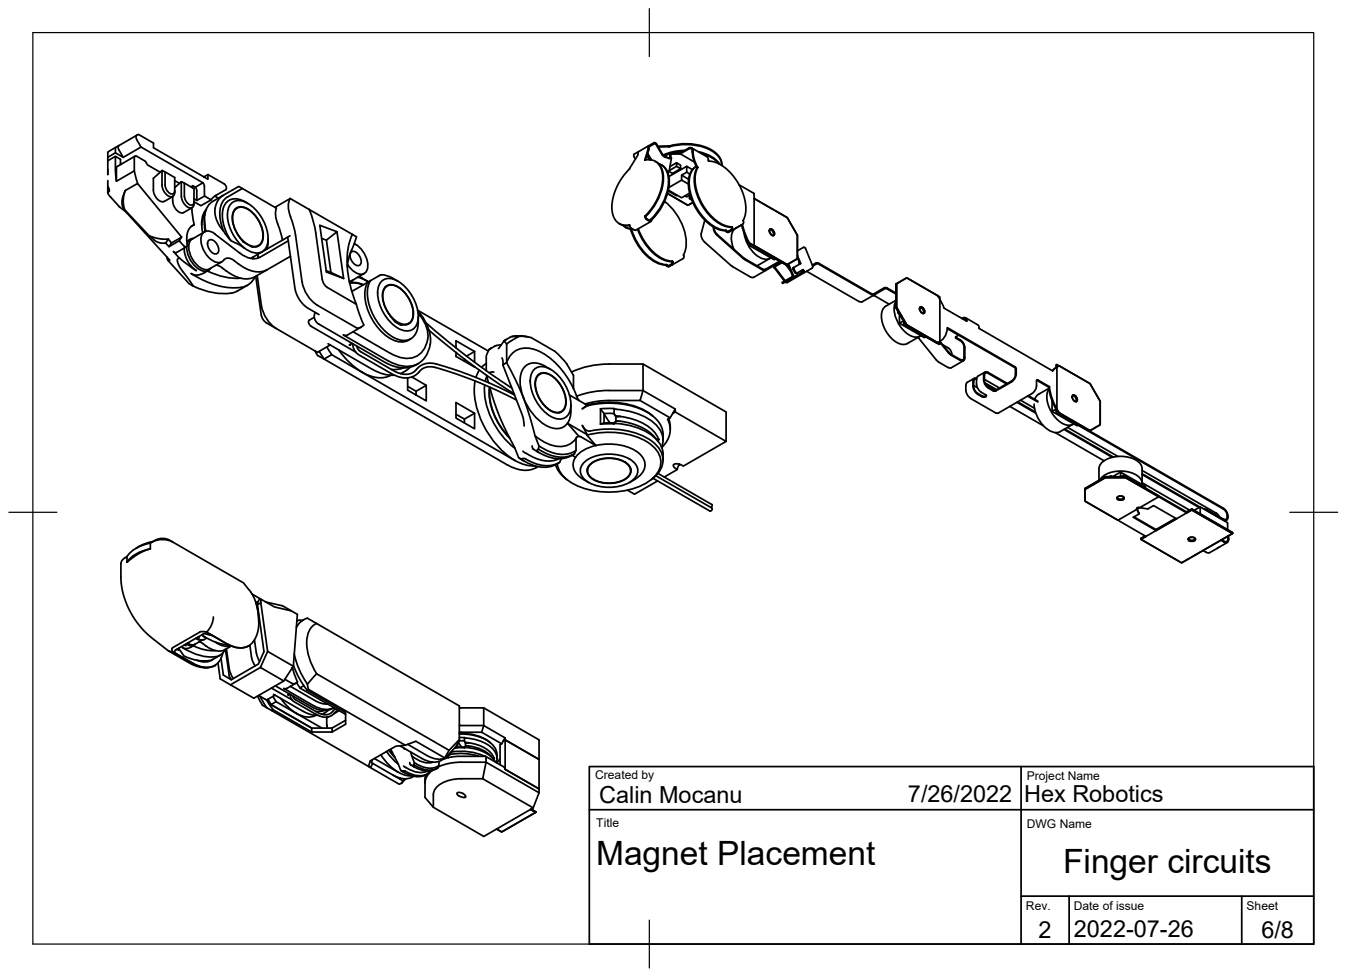
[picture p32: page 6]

Created by 7/26/2022 Calin Mocanu | Project Name Hex Robotics

Title Magnet Placement | DWG Name Finger circuits

Rev. | Date of issue | Sheet

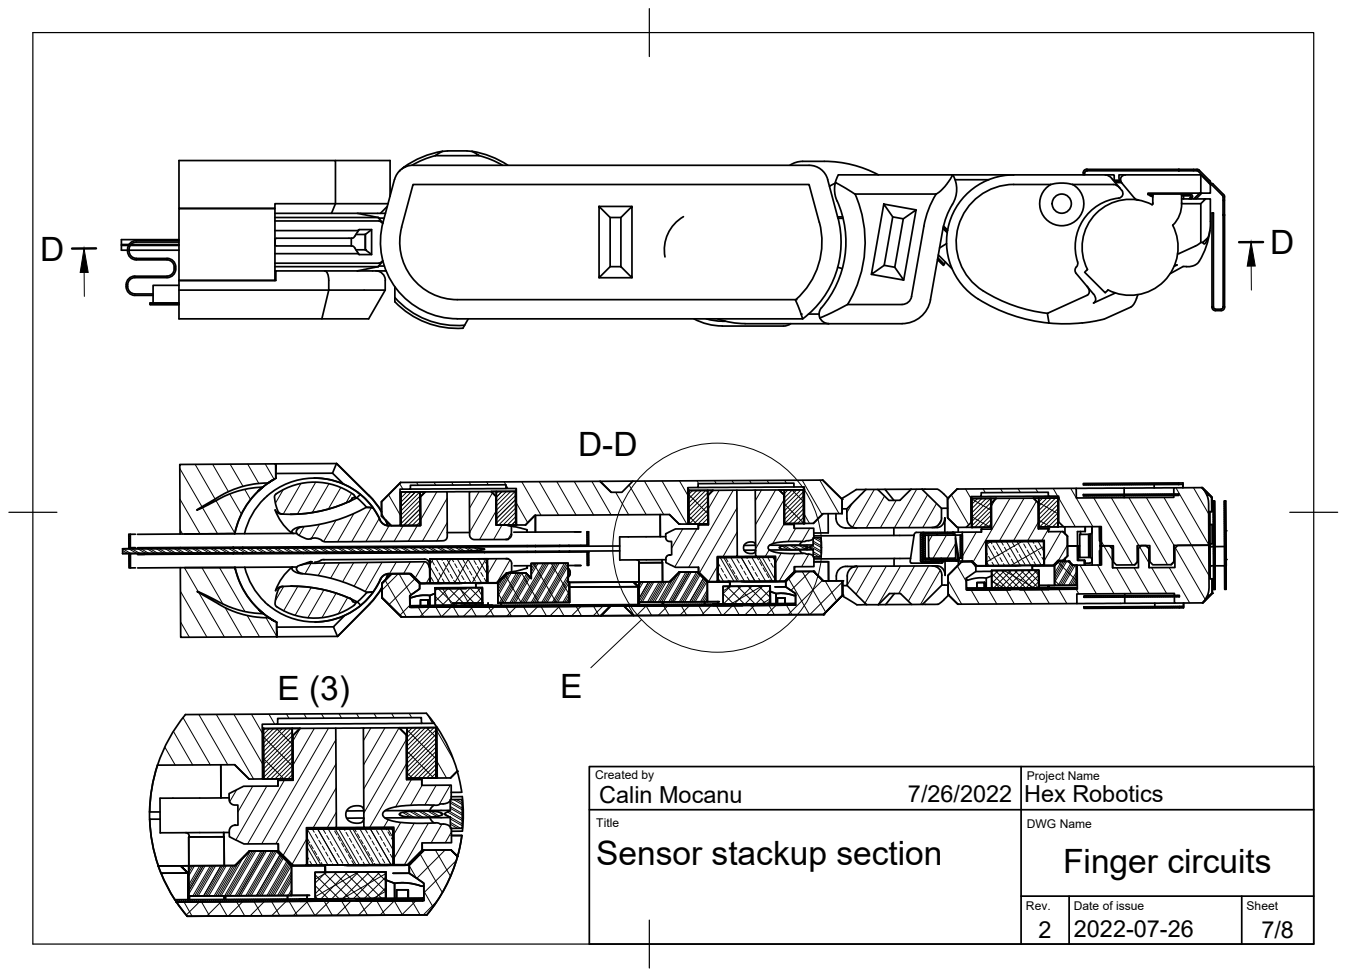
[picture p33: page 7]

Created by 7/26/2022 Calin Mocanu | Project Name Hex Robotics

Title Sensor stackup section | DWG Name Finger circuits

Rev. | Date of issue | Sheet

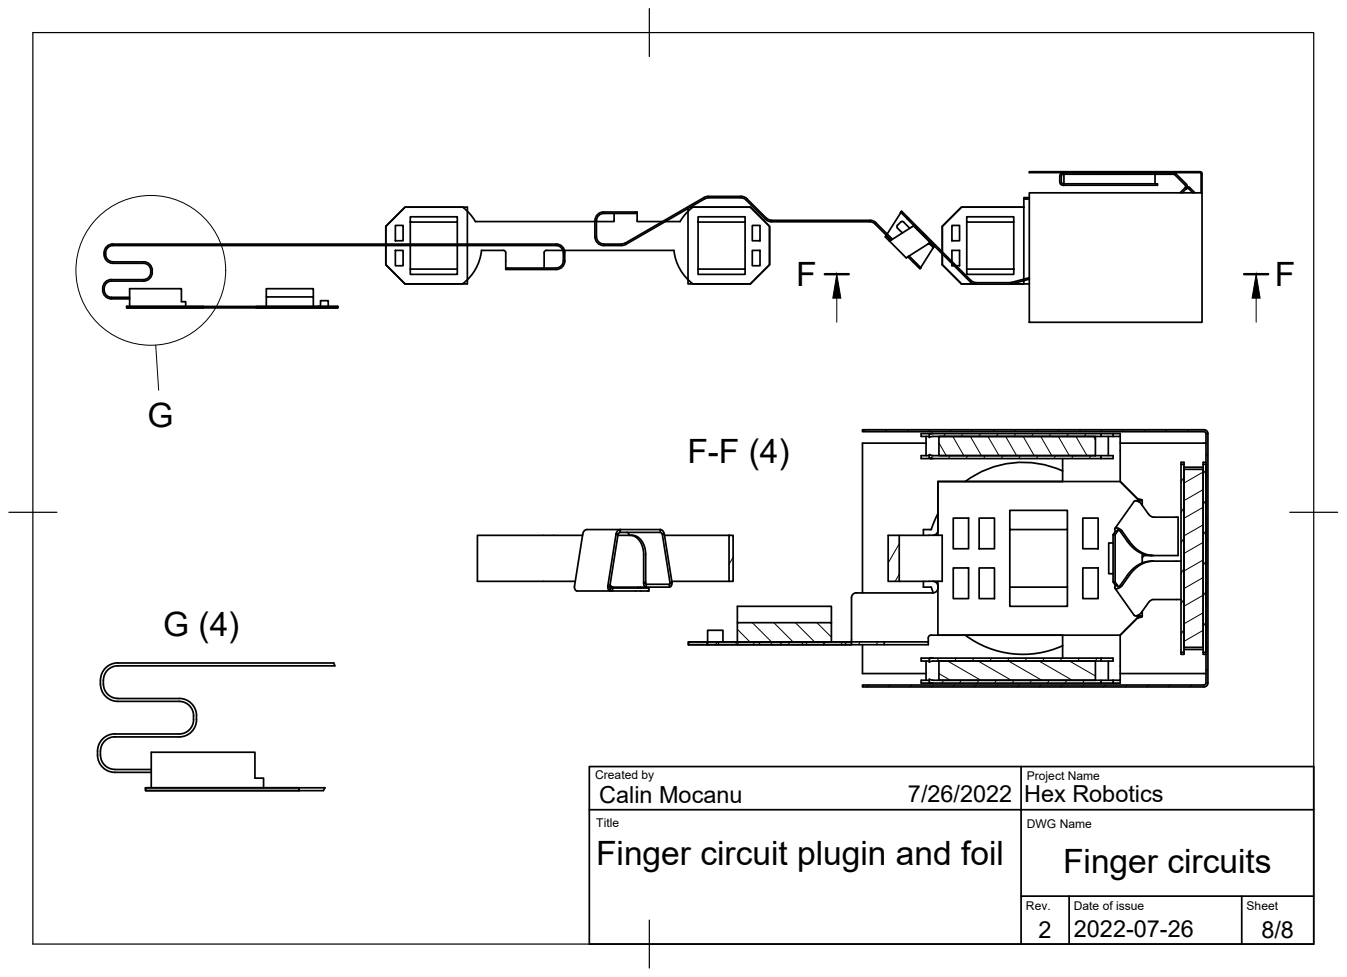
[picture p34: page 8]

Created by 7/26/2022 Calin Mocanu | Project Name Hex Robotics

Title Finger circuit plugin and foil | DWG Name Finger circuits

Rev. | Date of issue | Sheet

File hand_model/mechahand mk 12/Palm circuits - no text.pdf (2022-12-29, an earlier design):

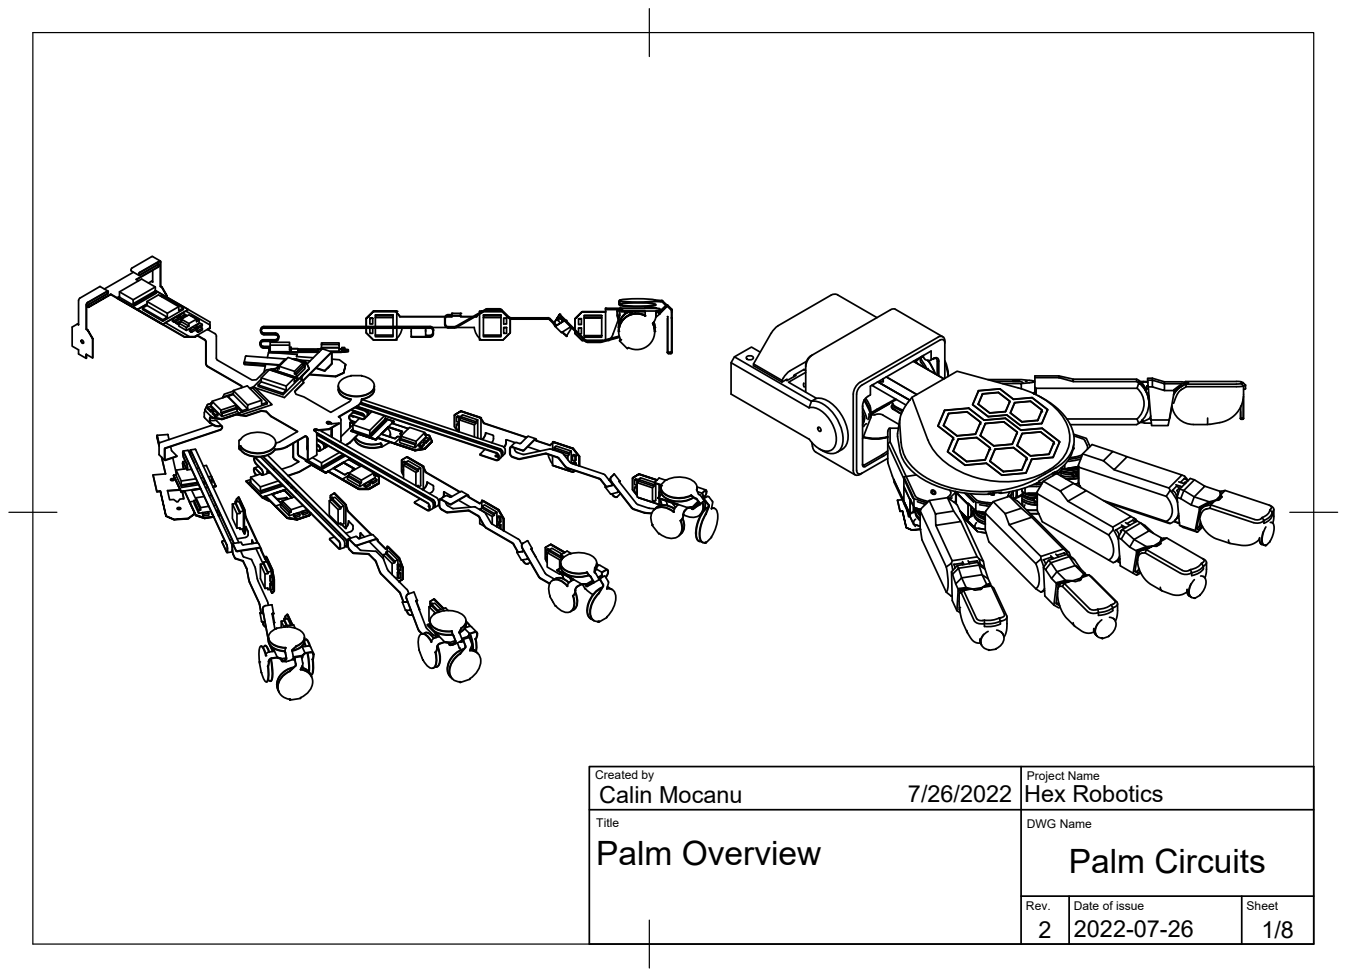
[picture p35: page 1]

Created by 7/26/2022 Calin Mocanu | Project Name Hex Robotics

Title Palm Overview | DWG Name Palm Circuits

Rev. 2 | Date of issue 2022-07-26 | Sheet

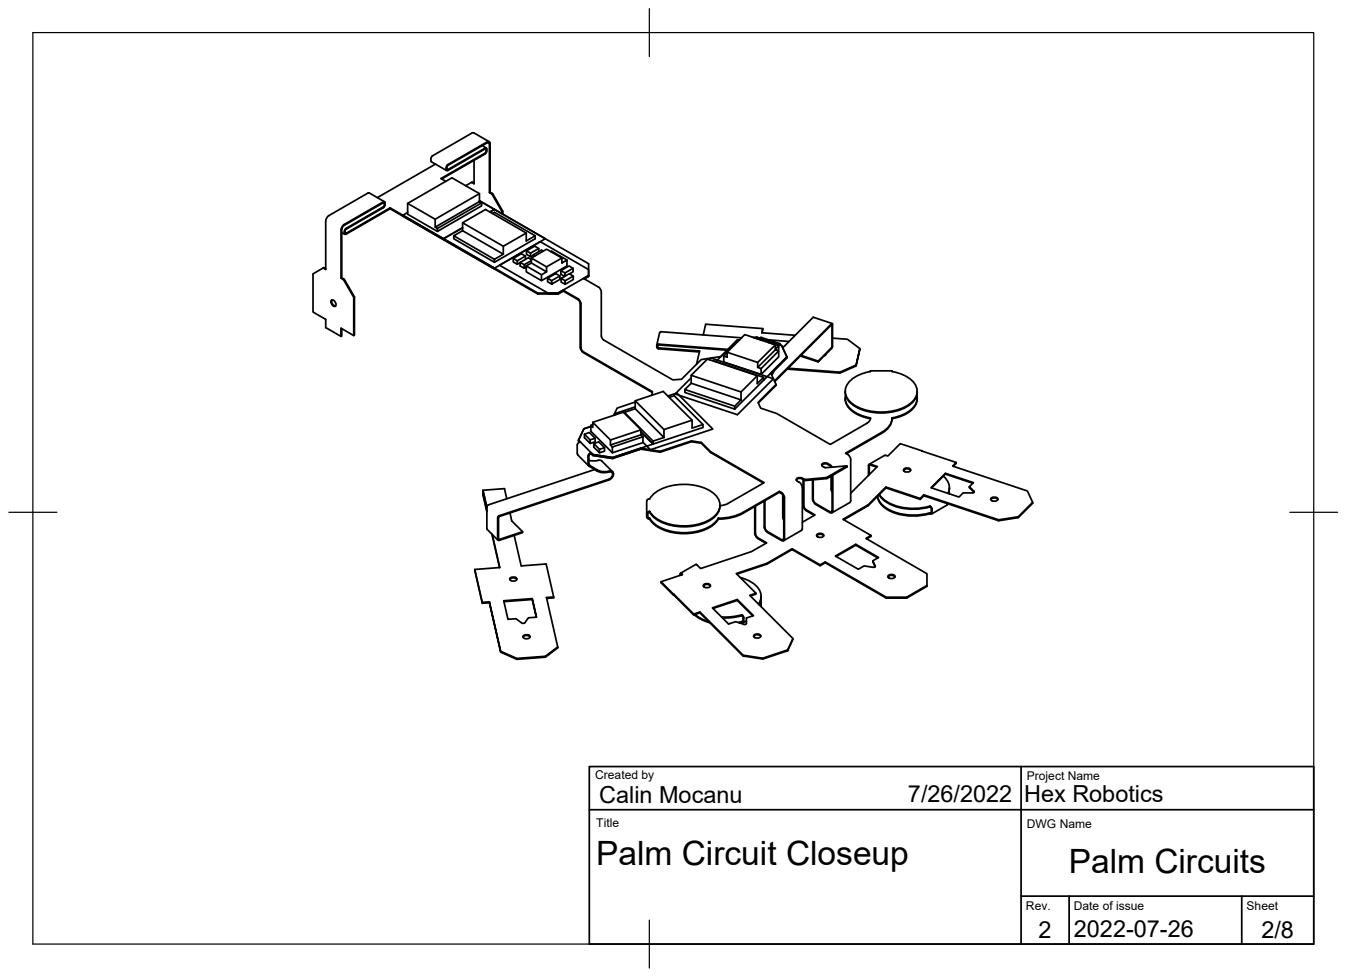
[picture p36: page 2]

Created by 7/26/2022 Calin Mocanu | Project Name Hex Robotics

Title Palm Circuit Closeup | DWG Name Palm Circuits

Rev. | Date of issue | Sheet


Created by 7/26/2022 Calin Mocanu | Project Name Hex Robotics

Title Pivot Joints | DWG Name Palm Circuits

Rev. | Date of issue | Sheet


Created by 7/26/2022 Calin Mocanu | Project Name Hex Robotics

Title Palm Force Sensors | DWG Name Palm Circuits

Rev. | Date of issue | Sheet


Created by 7/26/2022 Calin Mocanu | Project Name Hex Robotics

Title Wrist Differential Joint | DWG Name Palm Circuits

Rev. | Date of issue | Sheet


Created by 7/26/2022 Calin Mocanu | Project Name Hex Robotics

Title Wrist Differential Detail | DWG Name Palm Circuits

Rev. | Date of issue | Sheet


Created by 7/26/2022 Calin Mocanu | Project Name Hex Robotics

Title Finger circuit plugin palm | DWG Name Palm Circuits

Rev. | Date of issue | Sheet


Created by 7/26/2022 Calin Mocanu | Project Name Hex Robotics

Title Wrist Differential Section | DWG Name Palm Circuits

Rev. | Date of issue | Sheet

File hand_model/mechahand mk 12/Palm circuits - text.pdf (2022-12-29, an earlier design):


Created by 7/26/2022 Calin Mocanu | Project Name Hex Robotics

Title Palm Overview | DWG Name Palm Circuits

Rev. 2 | Date of issue 2022-07-26 | Sheet


Created by 7/26/2022 Calin Mocanu | Project Name Hex Robotics

Title Palm Circuit Closeup | DWG Name Palm Circuits

Rev. | Date of issue | Sheet


Created by 7/26/2022 Calin Mocanu | Project Name Hex Robotics

Title Pivot Joints | DWG Name Palm Circuits

Rev. | Date of issue | Sheet


Created by 7/26/2022 Calin Mocanu | Project Name Hex Robotics

Title Palm Force Sensors | DWG Name Palm Circuits

Rev. | Date of issue | Sheet


Created by 7/26/2022 Calin Mocanu | Project Name Hex Robotics

Title Wrist Differential Joint | DWG Name Palm Circuits

Rev. | Date of issue | Sheet

Tendon guide

Insert keeps circuit and
rotation encoder in place

Bevel gear with just
7-11 teeth

Clip with rotation sensor that
measures position of bevel gear
with respect to side bracket.

Tendon tie points

Rotational position encoder,

circuit leads up (not shown in closeup)

Clip holes Clip hooks

Created by 7/26/2022 Calin Mocanu | Project Name Hex Robotics

Title Wrist Differential Detail | DWG Name Palm Circuits

Rev. | Date of issue | Sheet


Finger circuit plugs into palm connector

Finger circuit end folded for assembly

Created by 7/26/2022 Calin Mocanu | Project Name Hex Robotics

Title Finger circuit plugin palm | DWG Name Palm Circuits

Rev. | Date of issue | Sheet

Roll bearings; Clip section

Bevel gear meshes with top central gear.
1. When the bevel gears on either side rotate opposite
each other the top gear also rotates, causing yaw motion.
2. When bevel gears rotate together, the whole mechanism
rotates, pitching the palm up or down.

Yaw bearings
Bevel gear bearing

Bevel gear tendon channel

Circuit with strain relief fold

U-joint crosshaft. Connects the
roll bearings to the yaw bearings.
Hole in the middle of wrist for tendons.

Bevel gear tendon guide

Side brackets mount into forearm

Reference magnet (rigidly connected to forearm)

Rotational Position Encoder clipped into side bevel gear.

Created by 7/26/2022 Calin Mocanu | Project Name Hex Robotics

Title Wrist Differential Section | DWG Name Palm Circuits

Rev. | Date of issue | Sheet

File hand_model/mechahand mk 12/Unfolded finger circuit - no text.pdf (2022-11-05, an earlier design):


Created by 7/26/2022 Calin Mocanu | Project Name Hex Robotics

Title Unfolded Finger Circuit | DWG Name Unfolded Finger Circuit

Rev. 2 | Date of issue 2022-07-26 | Sheet 1/1

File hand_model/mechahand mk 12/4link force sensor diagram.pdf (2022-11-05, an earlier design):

Proximal segment; Middle segment; Tip compression (force on nail area); No load case, bent pose; Tip extension (force on fingerprint area); Fingertip mechanics, straight pose; The finger tip is a 4 link bar assembly that constrains the

movement of the distal joints. The 4 links comprise 3 rigid
segments and a 4th semi-rigid segment denoted by the zig-zag line.

Distal segment (finger tip)

Active joint driven by motors.

Passive joint, driven by 4 bar linkage.

Semi-rigid middle segment lever

Force applied on the fingertip base
causes the semi-rigid lever to stretch
allowing the passive joint to extend
further while the active joint is fixed.

Force applied on the top of the finger
compresses the lever segment. We
can compute the torque applied by
measuring both joint angles relative
to the no-load condition.

When no load is applied to the fingertip the
angle of the passive joint can be computed from
the angle of the driven joint and the segment lengths.

Created by 5/31/2022 Calin Mocanu | Project Name Hextech mechahand mk 12

Title Fingertip force sensor | DWG Name 4link force sensor diagram

Rev. 2 | Date of issue 2022-03-04 | Sheet 1/1

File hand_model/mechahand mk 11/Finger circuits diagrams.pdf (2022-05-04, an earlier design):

Distal segment; Middle segment; Proximal segment; Metacarpal segment; Rotational encoder 2

Connector to palm circuit

Knuckle gimbal segment

Rotational encoder 3
Strain-relief loops

Split circuit strip
Rotational encoder 4

Middle segment knot
Rotational encoder 1

Part of palm circuit

Tip force sensors

Created by Calin Mocanu 2022-02-07 | Project Name Hextech mechahand mk 11

Title 3D finger view: left - flexible finger circuit right - finger structure | DWG Name Finger circuits diagrams

Rev. 2 | Date of issue 2022-03-04 | Sheet

Extra length for assembly; Split circuit strip fits through knuckle gimbal segment; Rotational encoders

and accomodates 2 rotational degrees of freedom.

Tip force sensors

Connector to palm circuit
Part of palm circuit

Strain relief loops

Middle segment knot

Force sensor chips
embedded in finger tip

Magnets for rotational encoders

Plastic clips to fix circuit in place

Middle segment lever

Created by Calin Mocanu 2022-02-07 | Project Name Hextech mechahand mk 11

Title Side view of finger: top - flexible finger circuit buttom - partial assemby | DWG Name Finger circuits diagrams

Rev. 1 | Date of issue 2022-03-04 | Sheet

FORCE SENSORS

Ancillary sensor circuitry nestled
within finger tip cavity

"Nail" force sensor

Folds needed to place the sensors
in the correct orientation in space

Distal tip force sensor

Ancillary sensor circuitry

Ground electrode facing the outside
and shielding the active electrode

Double sided adhesive tape or other soft
material sandwiched between electrodes

Active capacitive electrode

Created by Calin Mocanu 2022-02-07 | Project Name Hextech mechahand mk 11

Side force sensors
(one on each side)

Title Force sensor closeup | DWG Name Finger circuits diagrams

Rev. 1 | Date of issue 2022-03-04 | Sheet


The tip is driven by a tendon actuated joint and a second
passive joint linked to the former through the flexible
middle segment lever.

This construction forms a four-bar linkage with a well
defined relationship between the 2 rotation positions. By
measuring both positions we can infer the elongation of
the flexible lever and the force on the finger tip.

Cavity for the lever arm swing.

Middle segment flexible lever (bar no. 4). This lever
deforms when there is a force acting on the tip.

Distal rotation joint is passively driven

by the flexible lever. Middle rotation joint is actively

driven by tendons.

Distal segment (bar no. 3)

Middle segment (bar no. 2)

Proximal segment (bar no. 1)

Created by Calin Mocanu 2022-02-07 | Project Name Hextech mechahand mk 11

Title Four-bar linkage force sensor | DWG Name Finger circuits diagrams

Rev. | Date of issue | Sheet


Plastic clips hold the circuit in place.

Created by Calin Mocanu 2022-02-07 | Project Name Hextech mechahand mk 11

Title Circuit clips | DWG Name Finger circuits diagrams

Rev. | Date of issue | Sheet

3D finger view; Magnet for distal joint.; Sensor for distal joint.

The magnetic rotational position sensors measure the angle of
a diametrically polarized magnet placed in close proximity to the
center of the sensor.

Sensor for middle joint.

Magnet for middle joint.

Magnet for pitch joint.

Sensor for pitch joint.

Sensor for yaw joint.

Magnet for yaw joint.

Knuckle gimbal segment. Because of space constraints the yaw
and pitch axis of the knuckle are separated by a short distance.

Created by Calin Mocanu 2022-02-07 | Project Name Hextech mechahand mk 11

Title Magnet placement | DWG Name Finger circuits diagrams

Rev. | Date of issue | Sheet

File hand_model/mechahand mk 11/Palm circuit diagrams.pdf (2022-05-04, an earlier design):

Differential wrist joint; inside the palm without any visible wiring.

Electronic circuit and sensors are nestled

Position encoders for
differential wrist joint

Force sensitive palm cover

Force sensors for palm cover

Pinky and thumb pivot on an extra axis to allow
for opposable thumb and improve grasping.

Connector to finger circuit

Created by Calin Mocanu 2022-03-05 | Project Name Hextech mechahand mk 11

Pinky and thumb pivot position encoders

Title 3D palm view: left - flexible palm circuit right - palm structure | DWG Name Palm circuit diagrams

Rev. 1 | Date of issue 2022-03-04 | Sheet

Ancillary circuitry

Connector to forearm controller

Position encoders placed inside
the differential wrist joint gears

Relief loops for wrist differential
to accomodate small rotations of
the differential gears

Force sensors for top palm cover
(palm cover rests on pegs on
top of these sensors)

Position encoder for the pinky pivot joint
(encoder is connected to joint axis
through perpendicular bevel gears)

Flap affixes circuit into the structure
Holes in the circuit allows finger
tendons to pass through

Relief loop for pinky pivot rotational joint

Folds re-orient the pinky circuit
section into the proper orientation

Force sensors for bottom palm

Folded circuit section allows the bottom
to elongate to accomodate assembly

Created by Calin Mocanu 2022-03-05 | Project Name Hextech mechahand mk 11

Title 3D palm circuit | DWG Name Palm circuit diagrams

Rev. 1 | Date of issue 2022-03-04 | Sheet

Tendon holes

Pinky pivot joint is inline with ring finger
and protected below the palm cover

Thumb pivot enables the
opposable thumb pose

Tendons connected to motors in the forearm
engage with the guiding bevel gear on top.

Bevel gear pairs translate the movement from the tendons
to the opposable thumb axis and pinky pivoting axis.

Magnet embedded inside the bevel gear
is the reference for rotational encoder.
Rotational position encoders measures the
position of the guiding bevel gear; which
is linked to the position of the opposable
thumb and pinky pivot rotational axis.

Opposable thumb rotation axis is directly
in line with index finger, allowing tendons
to pass through the center of the bearing.

Created by Calin Mocanu 2022-03-05 | Project Name Hextech mechahand mk 11

Title Thumb and pinky pivot joints | DWG Name Palm circuit diagrams

Rev. | Date of issue | Sheet


The palm circuit contains capacitive force
sensors under the top and bottom covers.

Plastic pegs on the palm cover transmit
forces directly to the force sensors.

Top facing capacitive force sensors.

Bottom facing capacitive force sensors.

Recess in the bottom cover for the force sensor.

Created by Calin Mocanu 2022-03-05 | Project Name Hextech mechahand mk 11

Title Palm force sensors | DWG Name Palm circuit diagrams

Rev. | Date of issue | Sheet


Magnet embedded in wrist braket is
the reference for the rotational sensor.
Wrist bracket mounted to the forearm.

Bevel gear of differential wrist joint.

Position sensors embedded in bevel gear.
Strain relief loops allows the position
sensors to rotate with the bevel gear
without tearing the circuit.

Differential joint allows wrist to move with 2 degrees of
freedom, and bevel gear configuration leaves room
for wiring and tendons to pass through the center.

Recess for the circuit.

The position sensor in the bevel gear
is held in place by a plastic clip.

Created by Calin Mocanu 2022-03-05 | Project Name Hextech mechahand mk 11

Title Wrist differential joint | DWG Name Palm circuit diagrams

Rev. | Date of issue | Sheet

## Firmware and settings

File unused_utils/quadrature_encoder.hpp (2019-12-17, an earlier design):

#pragma once

#include "Arduino.h"
#include "esp32-hal-gpio.h"
#include "esp_attr.h"

// Inspired by code in:
// https://makeatronics.blogspot.com/2013/02/efficiently-reading-quadrature-with.html

const int8_t encoder_lookup_table[] = {
   0, -1,  1,  0,
   1,  0,  0, -1,
  -1,  0,  0,  1,
   0,  1, -1,  0};

void IRAM_ATTR encoder_interrupt(void * arg);

struct Encoder {
  const gpio_num_t a;
  const gpio_num_t b;
  volatile int position = 0;
  volatile bool a_value;
  volatile bool b_value;
  volatile unsigned long last_interrupt_micros;

  int n_interrupts = 0;
  int last_position = 0;
  int min_delay = 10;

  // Set the encoder to be an active LOW or active HIGH state.
  const bool active_state;

  Encoder(const gpio_num_t a, const gpio_num_t b, const bool active_state = HIGH) : a(a), b(b), active_state(active_state) {}

  void begin(){
    pinMode(a, active_state == HIGH ? INPUT_PULLDOWN : INPUT_PULLUP);
    pinMode(b, active_state == HIGH ? INPUT_PULLDOWN : INPUT_PULLUP);

    a_value = digitalRead(a) == active_state;
    b_value = digitalRead(b) == active_state;
    last_interrupt_micros = micros();

    attachInterruptArg(a, encoder_interrupt, this, CHANGE);
    attachInterruptArg(b, encoder_interrupt, this, CHANGE);
  }

  void end() {
    detachInterrupt(a);
    detachInterrupt(b);
  }

  int collect_change(){
    int change = position - last_position;
    last_position += change;
    return change;
  }
};

void IRAM_ATTR encoder_interrupt(void * arg) {
  Encoder & encoder = *static_cast<Encoder*>(arg);

  // Debounce interrupts if within a very short time.
  const unsigned long diff = micros() - encoder.last_interrupt_micros;
  // Note that when micros <  last_interrupt_micros because of the
  // time overflow, then diff should also underflow into a high value.
  if (diff < encoder.min_delay) return;

  // Flip the states if we use pull-up as it's active LOW.
  const bool active_state = encoder.active_state;

  bool new_a_value = digitalRead(encoder.a) == active_state;
  bool new_b_value = digitalRead(encoder.b) == active_state;

  const uint state =
    encoder.a_value << 3 |
    encoder.b_value << 2 |
    new_a_value << 1 |
    new_b_value;

  encoder.position += encoder_lookup_table[state];

  encoder.a_value = new_a_value;
  encoder.b_value = new_b_value;

  encoder.last_interrupt_micros = micros();

}

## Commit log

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2019-08-01 Remember which pin is in an error state and disable drive.
2019-08-12 Add fps measurement and error per pin getters.
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2019-10-18 Fix pin errors to be indexed by the input index.
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2019-10-22 Enable driver comms for all chips, and strengthen i2c error checks.
    The problem with the drivers not communicating properly was that the address pin 0
    was connected to the error LED and therefore pulled low. This set the wrong address on the driver.
    Replacing the resistor with a 10K ohm one fixes the problem for now, but it needs a chip redesign.
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2019-10-24 Option to save or reset joint configuration.
2019-10-24 Can't fix ESP input voltage problem in code, write todo for next chip version.
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2019-10-31 Redesign PCB boards.
2019-12-17 Fix buttons and wheels.
    [button.hpp, quadrature_encoder.hpp]
2019-12-17 Redesign circuits into a single 24 channel driver.
    [24+Channel+PCB.pcbdoc, BOM_Hextech 24 DC Driver.csv, PickAndPlace_24 Channel PCB.csv]
2019-12-20 Adjust PCB to fix button problem and order.
    [24+Channel+PCB.pcbdoc, BOM_Hextech 24 DC Driver.csv, PickAndPlace_24 Channel PCB.csv]
2020-01-13 Setup esp-idf project for 24drivers, and implement motor drivers logic.
    [BOM_Hextech 24 DC Driver.csv, PickAndPlace_24 Channel PCB.csv]
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2020-01-23 Work-around issues switching WiFi from AP to STA mode.
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2020-01-27 Fix timer's frame limititing and print web fps.
2020-01-28 Implement power command; motors can now be controller.
    [partitions.csv]
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2020-01-30 Implement some reconnect logic; still need to fix "Too many messages queued" on the ESP32.
2020-02-10 Fix PID bug.
2020-02-12 Upload 3D models for mechahand 2.
    [Base insert.stl, Base.3mf, Base.stl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]
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2020-02-12 Upload Fusion 360 design files for mechahand 4.
    [Actuated.stl, Casing.stl, Direct drive.f3z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]
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2020-02-18 Remodel finger joint to use better quality pots and torsion springs.
    [Actuated.stl, Base.stl, Cap.stl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]
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2020-04-01 Model mk5 hand. Hand with finger covers, and double side actuated nylon wires through PTFE tube guides, with individual spring tensioners.
    [2x Base.stl, 2xCasing.stl, Arm part 1.3mf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]
2020-04-01 Model hand mk6. Thinner tube guides with lighter spring tensioners and thicker finger covers.
    [Attachement.stl, Base to mid.stl, Base.stl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]
2020-04-01 Model hand mk7, the chosen one! Much less friction and more flexibility from tendons passing freely through middle of hand/wrist. Also design is much sturdier with proper bearings on every joint. Wri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
    [1st axis cap.stl, 1st axis.stl, 2nd axis cap.stl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]
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2020-04-13 Update PID behaviour for the integral term.
    Don't reset the integral at maximum power, just keep it constant. Clamp it to max power so it doesn't get unwiedly large. Also reset the integral when we cross the target; not just within threshold.
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2020-05-08 Iterate on hand design with mk 9 hand. Smaller, better, stronger.
    [1st axis.stl, 2nd axis clamp.stl, 2nd axis.stl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]
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2020-05-12 Fix closing the driver.
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2020-05-21 Copy over the motor system driving the tendons.
    [Casing.stl, Holder rod.stl, Spindle.stl]
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2020-06-08 Version 2 of the 24 driver PCB design.
    Many improvements since last version, fixing all issues in the todo:
    * Smaller design.
    * No motor caps.
    * Replace discountinued chip for motor current sensing.
    * Use a buck converter to allow for 24V input voltage, and increased efficiency.
    [BOM_Hextech 24 DC Driver.csv, PickAndPlace_24 Channel PCB.csv]
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2020-08-18 Model mk 10 of the hand. Easier assembly, less wrist strain, hidden cables.
    [1st axis.stl, 2nd axis clamp.stl, 2nd axis.stl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]
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2020-08-20 Print detailed worm gears sequentially.
    Also use larger layers, since small ones might just be introducing unnecesarry edges.
    Also randomize seam points, other settings will produce a rough side for the gear, and we don't like that.
    [Detail gears.3mf]
2020-08-22 Temporary fix the burnt diode, turn off by unplugging or low battery.
2020-08-22 Add burnt diode problem, welded button to TODO list.
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2020-08-27 Added missing item to BOM.
2020-08-28 Experimental tensioner via split in half interlocking spindle.
    [Knotting bead.3mf, Knotting bead.stl, Spindle top.stl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]
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2020-08-31 Update mk10 motor sytem, to use a fancy tensioner widget.
    [Casing.stl, Finger.3mf, Knuckle pivot.stl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]
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2020-10-08 Upload robot arm design using cycloid drives and 5010 brushless motors.
    [Actuated cap.stl, Actuated.stl, Cycloid half.3mf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]
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2020-10-08 Begin modelling mk 11 design. CorePY wrist, and tiny cycloid gearbox for coreless motors.
    [Actuated frame.stl, Back gimbal half.stl, Bottom spin.stl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]
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2021-01-17 Revert "Version arm model files."
    This reverts commit 73b2688b0209ff3b2680965f45239776016fa05b.
    [Actuated cap.stl, Actuated.stl, Cycloid half.3mf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]
2021-01-17 Revert "Revert "Version arm model files.""
    This reverts commit 0ae083be985bbfd5c3008eb4487a8988ee439563.
    [Actuated cap.stl, Actuated.stl, Cycloid half.3mf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]
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2021-01-17 Design strain wave differential gear and use it in new arm version.
    [Actuated mount.stl, Actuated spline.step, Actuated spline.stl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]
2021-01-17 Implement various planetary reduction stages, nothing working optimally.
    [Actuated cap.stl, Actuated frame.stl, Actuated tip.stl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]
2021-03-29 Model first iteration of the 4 joint finger.
    [Bot base.stl, Finger.3mf, Knuckle gimbal.stl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]
2021-04-13 Add stl files of the assembled finger and strain drive (for github preview).
    [Finger assembled.stl, Strain wave drive 42x assembled.stl]
2021-04-13 Add a landing page and pics for the strain wave drive.
    [Actuated spline.step, Flex spline 30x.stl, Flex spline.step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]
2021-07-05 Prototype a strain wave differential, it breaks because the flex cup flexes too much at the base...
    [Base mount.stl, Flex spline.stl, Gimbal structure.3mf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]
2021-07-05 Experiment with small measurable and retractable coils for the sensor glove.
    [6mm rod.stl, Cap.stl, Case.stl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]
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2021-07-05 Design flexible circuits for the finger and palm.
    [BOM_All fingers and roll sensor_2021-06-06.csv, BOM_Palm circuit_2021-06-06.csv]
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2021-10-11 Settle on high reduction strain wave design for arm base motors.
    [Flex spline.3mf, Flex spline.step, Flex spline.stl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]
2021-10-11 Experiment with miniature resin printed cycloid and a wire twisting reduction.
    Resin printed cycloid don't work cause too brittle and frictiony. Twisty reduction don't work because there's no reliable way to unwind the twist.
    [Cycloid.stl, Flex spline.stl, Housing.stl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]
2021-10-11 Update the model to correctly print a working prototype.
    [Bottom pressure pad.3mf, Covers.3mf, Finger.3mf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]
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2022-01-10 Rotate thumb, fine tune printing and finalize the case.
    Rotated thumb by 30 degrees compared to horizontal, makes the opposable thumb pose easier to achieve.
    Test-fit finger and circuit assembly, add brims to properly print fingertips.
    Make snap fit PCB case and pre-scale the whole casing size by 0.4% to adjust for shrinkage.
    [Bearings cap.stl, Bottom pressure pad.stl, Bottom structure.stl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]
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2022-01-25 Refine pieces to be printable and fit nicely.
    [Bearings cap.stl, Bottom pressure pad.3mf, Bottom pressure pad.stl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]
2022-03-07 Write short patent description and drawings.
    [Finger circuits diagrams.dwg]
2022-03-07 Small printing fixes for mk 11 parts.
    [Bottom pressure pad.stl, Main.stl, Palm 2.3mf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]
2022-03-07 Start designing mark 12 hand which has iterative improvements over mk 11.
    [Bearing peg.stl, Bot spindle.stl, Shaft interlock.dxf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]
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2022-05-04 Start a new hand version with new motors, box and wrist improvements.
    [Shaft interlock.dxf, Test bearing cap.stl, Test motor support.stl]
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2022-11-05 Experiment with TPU mesh for the potential sensor glove.
    [Mesh strip.3mf, Mesh strip.stl]
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2022-11-05 Begin work on mk13 hand with spring for the extension movement and a single wire for flexion.
    [Base bottom.stl, Base mid.stl, Base top.stl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]
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
